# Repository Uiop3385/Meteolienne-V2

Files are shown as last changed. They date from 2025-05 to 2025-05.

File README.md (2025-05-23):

# Meteolienne-V2

A project aiming to create an extra-efficient wind turbine, that's able to spin around to face the wind, and includes several sensors to add weather station capabilities.

It's also capable of generating up to 10W of power, and is entirely self-sufficient, thanks to an on-board battery and solar panel, and a sleeping system to save power.

Here are some pictures:  
View from the bottom

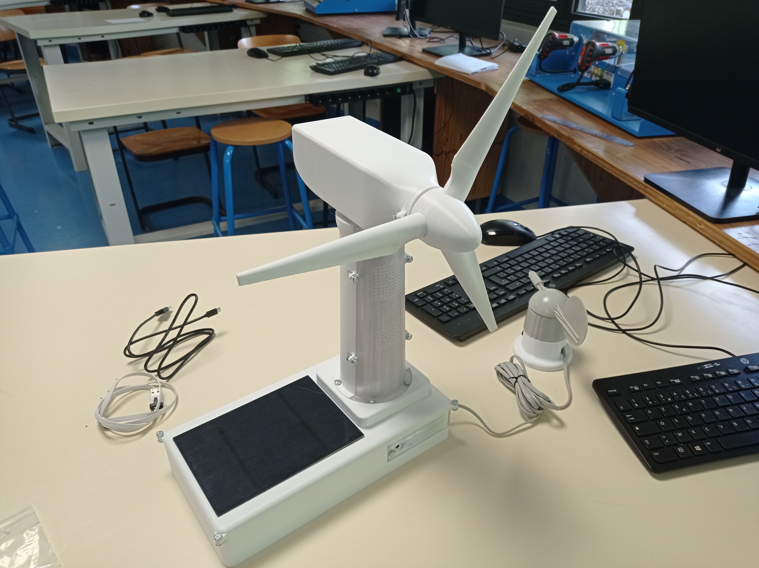
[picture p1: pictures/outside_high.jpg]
View from the top


## Disclaimer
If you're going to use any part of this project, please make sure you follow the terms of the licence. You can see a breakdown of them [here](https://choosealicense.com/licenses/mpl-2.0/).

## Info

This project is the successor to the [original Météolienne](https://github.com/Uiop3385/Meteolienne-V1) I've made. Compared to the first one:

- It's actually *somewhat* finished
- It communicates using WiFi and can be controlled through an app and web dashboard
- It implements the weather station capabilities
- It's far more energy efficient
- It generates power

The wireless connection is operated through Arduino IoT Cloud, using an Arduino MKR WiFi 1010 board. You'll need an account and a Maker subscription to make it work.

Some parts of this project, including variables in the code, part names in the CAD representation, etc, **are written in French**.

## Dashboards
Here are two images showcasing part of the two dashboards, the data one first, and the settings one after.

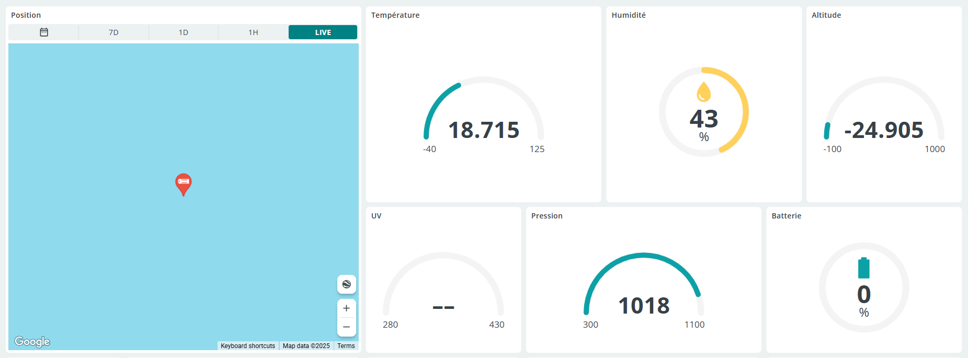
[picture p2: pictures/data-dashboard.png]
Data dashboard


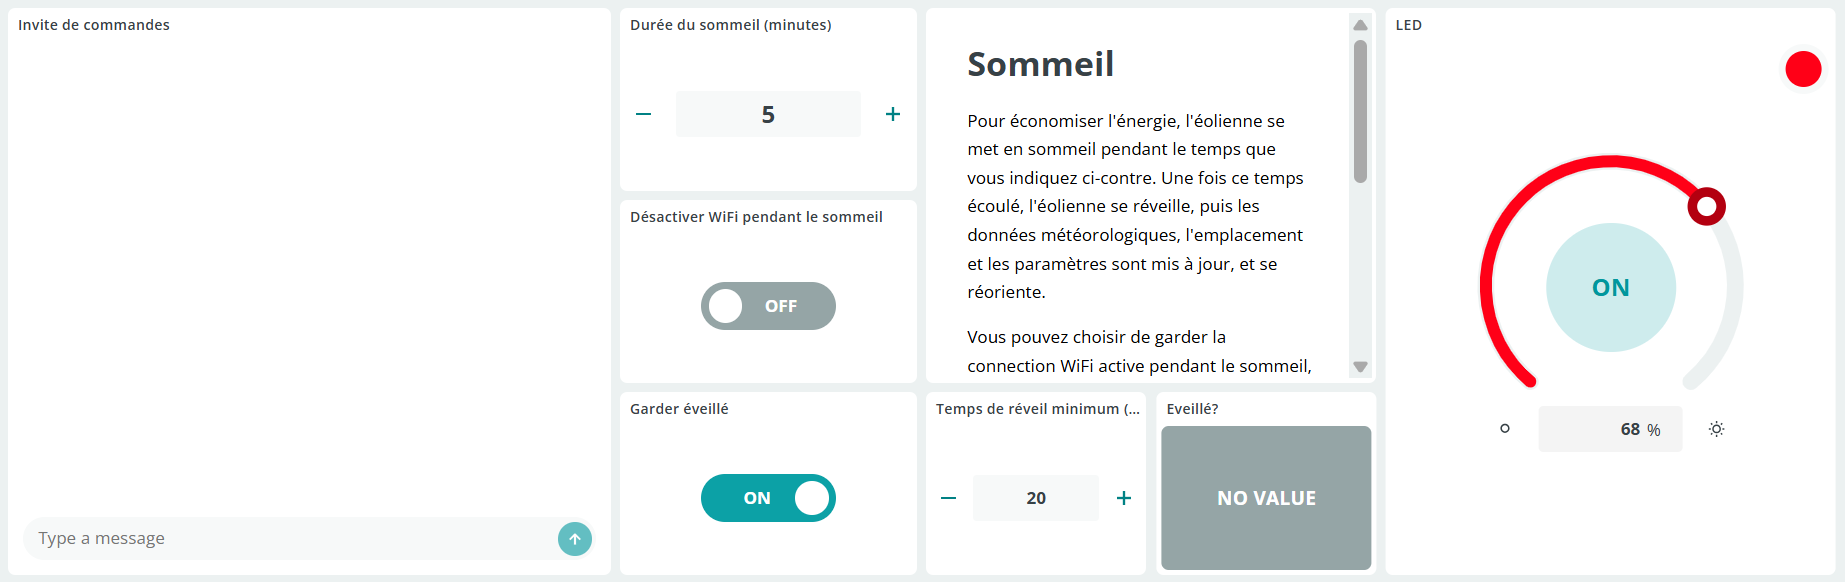
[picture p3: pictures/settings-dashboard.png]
Settings dashboard


These are the web dashboards. The mobile versions of them aren't shown here, but they're the same with a different layout to fit the size of a phone screen.

## Scripts
The files included in /scripts are not ready for use on the IoT Cloud editor. If you want to implement the code, dashboard, things and cloud variables, it's essential to use the template. If you're simply taking certain parts of the scripts, ignore this.

### Guide:
- Download meteolienne_template.tino in /scripts
- Access the Cloud Dashboard (https://app.arduino.cc)
- Go to Templates, then click on "Your Templates" at the top
- Select "Import local template (.tino)"
- Import the file you downloaded
- Then, press "Use template"
- You'll be asked to connect an Arduino MKR WiFi 1010

Once this is done, everything will automatically be copied over, and you're almost ready to upload! Just fill in the secrets tab with your WiFi credentials, and your ipdata API key for geolocation (you can get one free from their website, https://ipdata.co).

## Models
The entire wind turbine was modelled using Autodesk Fusion. You can access the .f3z from /models. If you're using a different CAD, there's also a .step you can use.

Alternatively, all parts of the wind turbine are available as .stl in /models/parts.

Render of the turbine from Fusion:
Realistic render of the wind turbine

The models were designed to be 3D printed. The ideal materials would be PETG and ASA, since they're strong, water resistant, and UV resistant. My prototype was made using PETG, with white filament for all parts but the mast cover and the IO shield. Those were printed in translucent filament.

## Components used
### Sensors
|Part name|Brand|Qty|
|--|--|--|
|MQ135 Air Quality sensor|Flying Fish|1|
|SEN0501 Environmental Sensor|DFRobot|1|
|NVGRLEX002 Wind vane + board|Lextronic|1|

### Other components
|Part name|Brand|Qty|
|--|--|--|
|C6045 Voltage Generator|cebekit|1|
|MKR WiFi 1010 board|Arduino|1|
|mBot Battery (Li-Po, 3.7V, 1800mAh)|Makeblock|1|
|28BYJ-48 Stepper Motor + Driver|N/A|1|
|S7V8F5 5V Voltage Regulator|Polulu|1|
|313070000 2.5W Solar Panel|Seeed Studio|1|

### Electronic components
|Type|Value/Ref|Qty|
|--|--|--|
|Resistor|220Ω|2|
|Resistor|1kΩ|4|
|Resistor|10kΩ|4|
|Resistor|15kΩ|2|
|Pushbutton|N/A|1|
|Capacitor|1000µF|1|
|LED|N/A|1|
|Diode|1N4007|6|
|Transistor|2N2222|4|

### Assembly parts:
|Type|ISO Reference|Value|Qty
|--|--|--|--|
|Bolt|ISO 4017|M4x10|19
|Nut|ISO 4035|M4|19|
|Screw|ISO 7046|M4x40|1|

And a bunch of jumper wires.

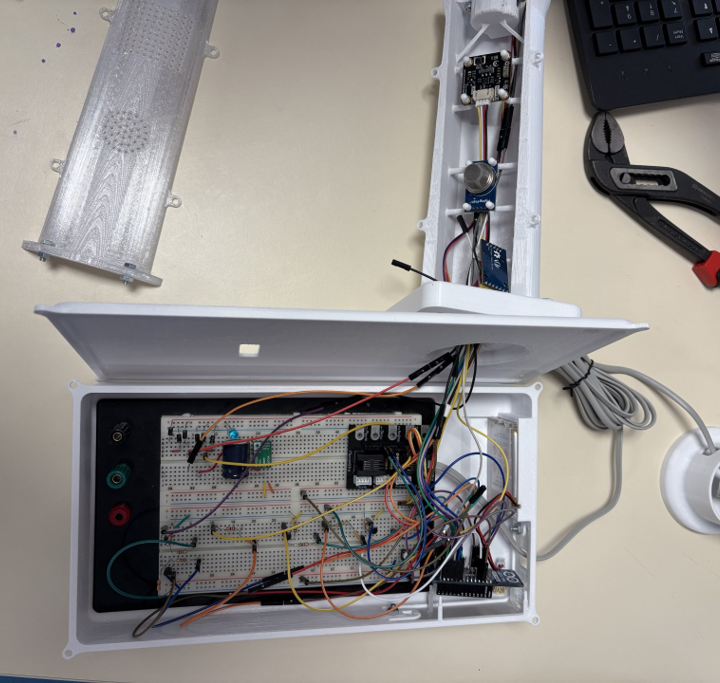
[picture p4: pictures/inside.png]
Inner wiring
Image of the inside:

## Oversights
While the project seems finished, there's still many things that are wrong with it. Here's a quick list of them:
- I can't actually get it to work. I'm unsure if the problem comes from my program or my board, but it won't let me upload it. The board no longer shows up on the computer outside of bootloader mode.
- Many components used rely on 5V, which I unsuspectingly hooked up to the 5V pin. However, this pin only outputs the 5V power coming from the USB. That means the board will never output this voltage from battery. The turbine is therefore not "self-sufficient".
- The wind near the ground is highly unstable. If you were to place the turbine on the ground, it would greatly struggle to pick up wind correctly. Not to mention, the wind vane would act very strangely too. It would need to be suspended much higher into the air for everything to function correctly.
- If wind speeds get too high, there's no protection to prevent the blades from spinning too fast and damaging the internals.
- There are several design flaws in my model. I only noticed them when assembling the turbine, and haven't fixed them since.
- Geolocation is, by design, highly inaccurate, since it's basing itself on IP address location. During testing, I could only ever get it to locate me in the same place in Germany (probably the location of the IoT Cloud servers). This could be mitigated by using Google's API.

## Assembly
I will not be providing any assembly instructions. You'll have to do with the information available here. Who would even want to recreate this anyway?

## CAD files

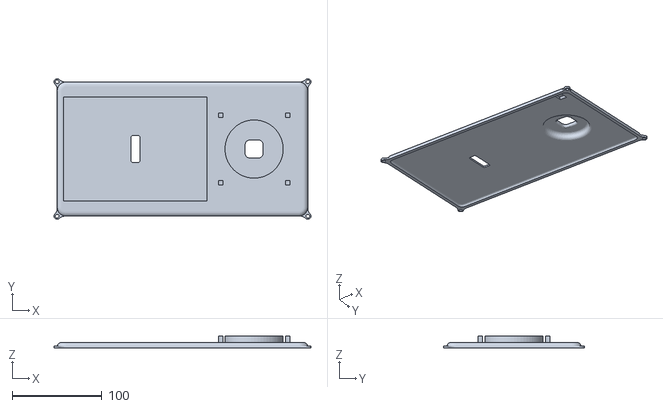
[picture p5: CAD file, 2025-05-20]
models/parts/Base Haute.stl
287.0 x 157.0 x 13.8

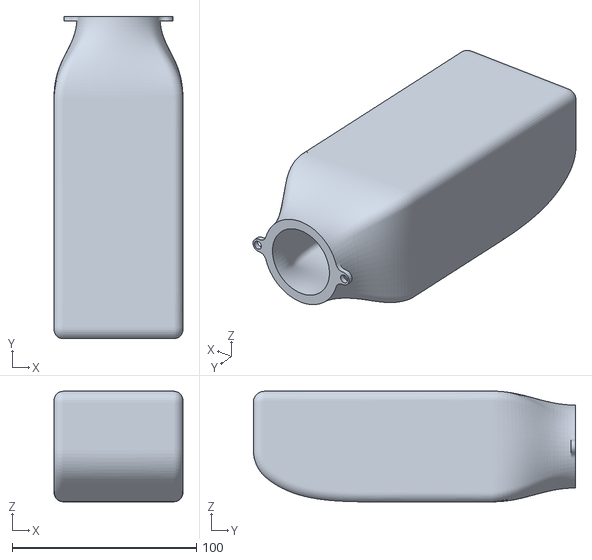
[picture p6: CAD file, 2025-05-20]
models/parts/Nacelle.stl
70.0 x 175.0 x 60.0

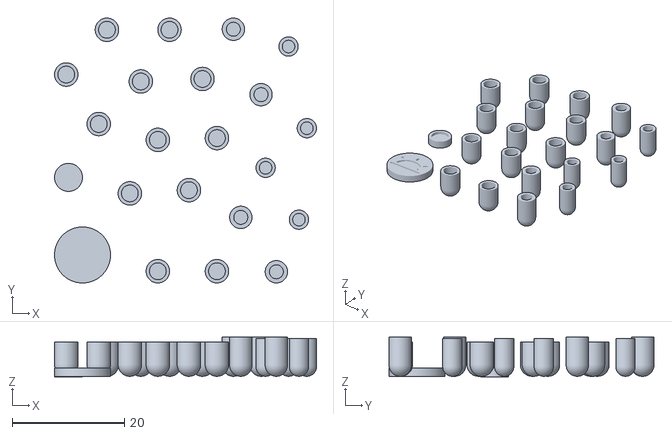
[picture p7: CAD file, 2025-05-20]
models/parts/Plaque Fixations v2.stl
46.8 x 47.3 x 7.10

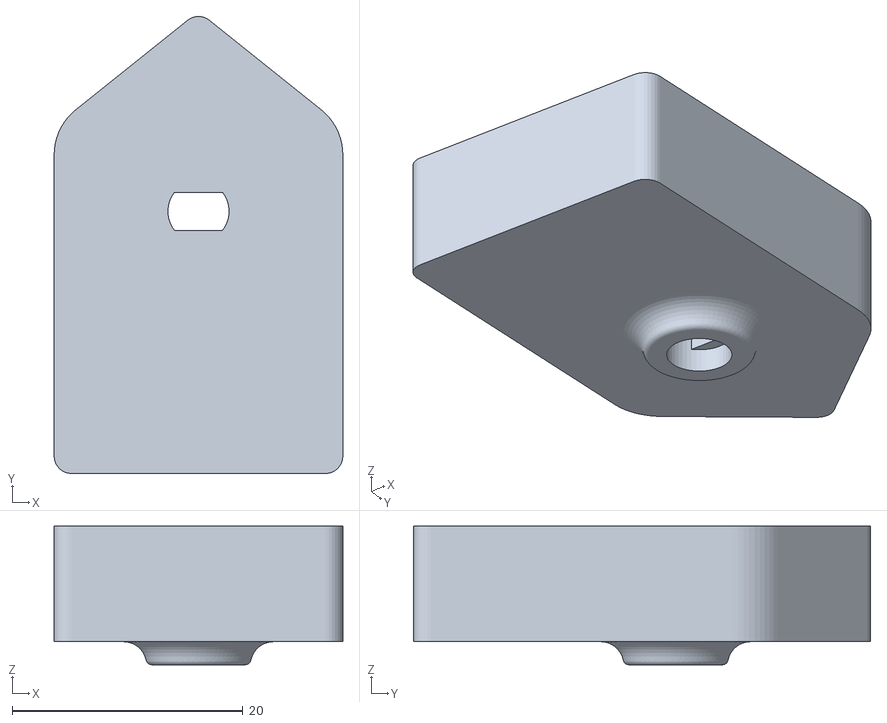
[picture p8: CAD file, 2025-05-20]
models/parts/Flèche.stl
25.0 x 39.6 x 12.0

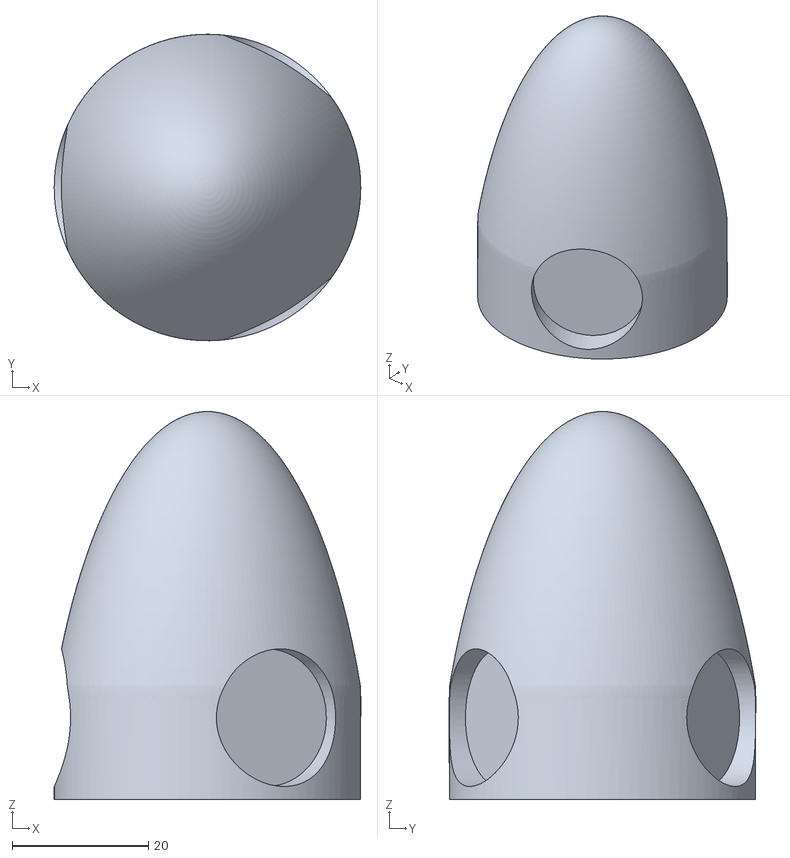
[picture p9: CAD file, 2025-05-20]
models/parts/Moyeu.stl
45.0 x 45.0 x 57.0

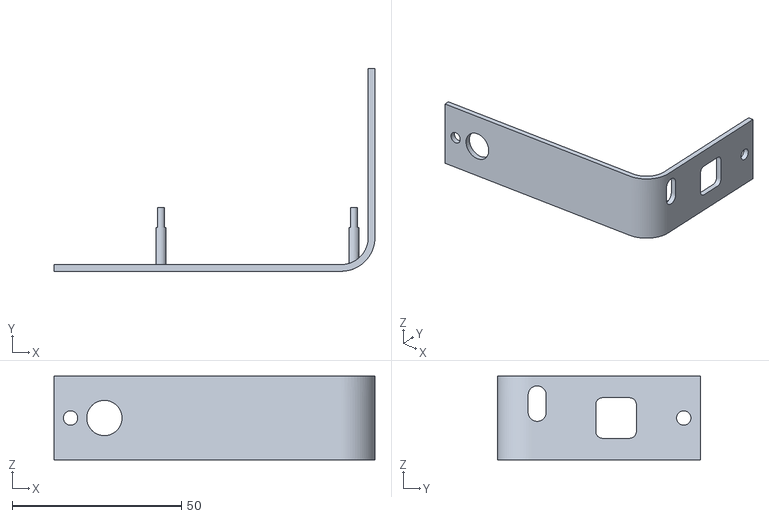
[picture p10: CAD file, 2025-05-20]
models/parts/IO Shield v2.stl
94.9 x 59.9 x 24.8

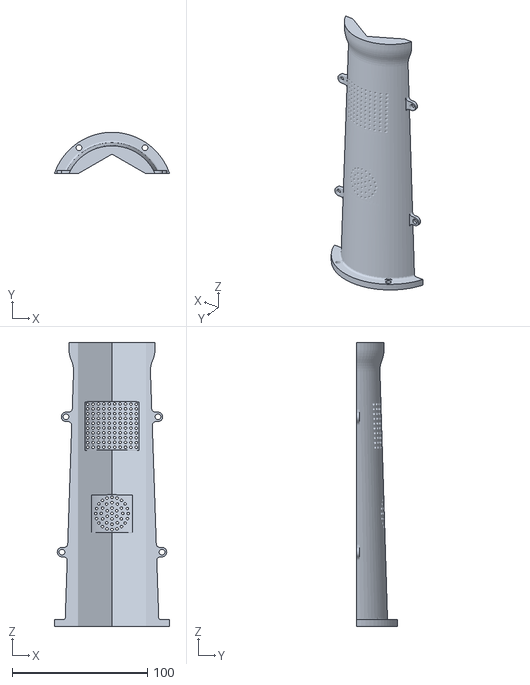
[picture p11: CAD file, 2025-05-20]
models/parts/Mât Secondaire.stl
85.2 x 30.5 x 210.0

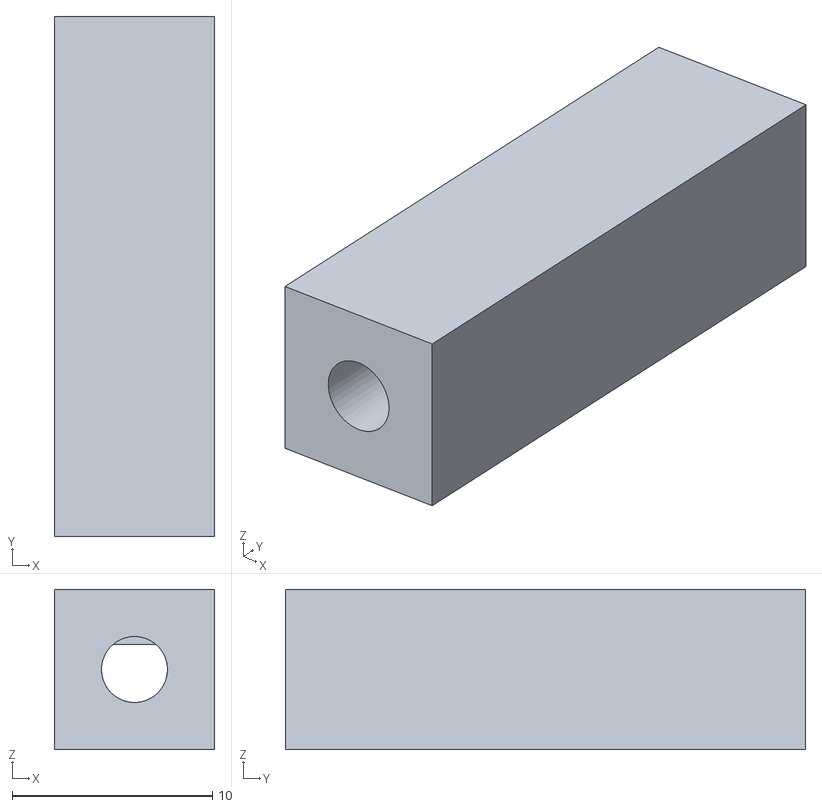
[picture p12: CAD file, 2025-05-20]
models/parts/Pavé.stl
8.00 x 26.0 x 8.00

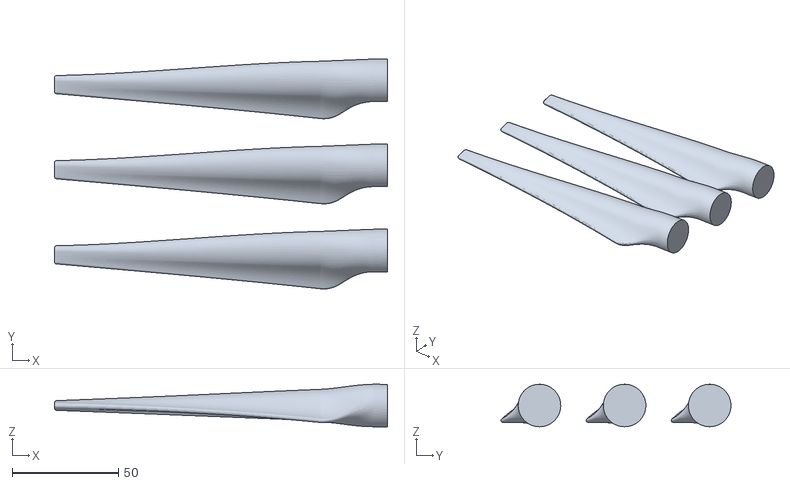
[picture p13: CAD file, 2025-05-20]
models/parts/Pales.stl
156.5 x 108.1 x 20.0

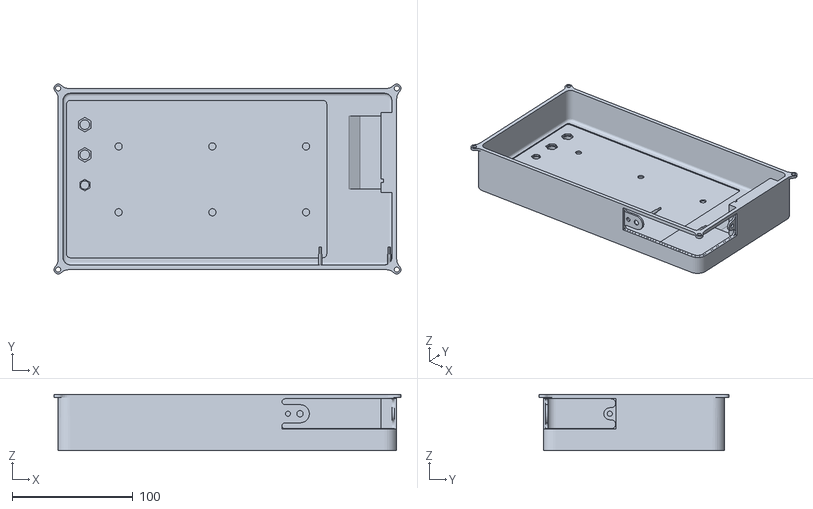
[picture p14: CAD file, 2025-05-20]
models/parts/Base Basse v2.stl
287.0 x 157.0 x 46.5

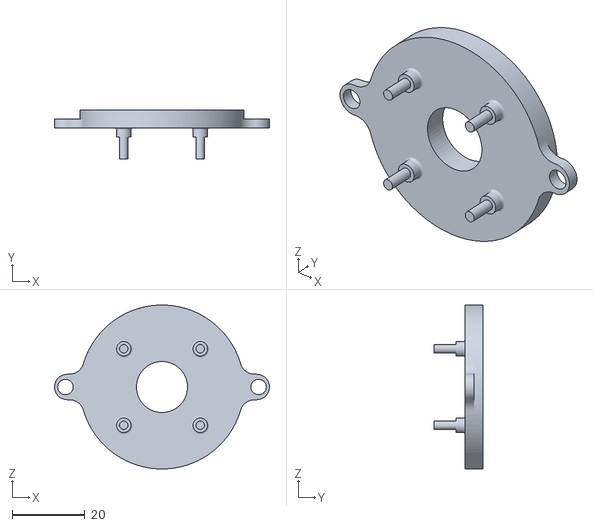
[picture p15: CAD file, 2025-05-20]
models/parts/Paroi Rotor 2.stl
59.0 x 13.5 x 45.0

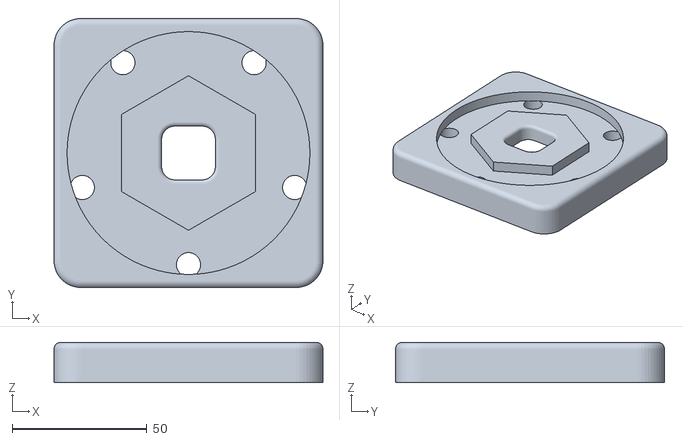
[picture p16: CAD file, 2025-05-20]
models/parts/Support Mât.stl
100.0 x 100.0 x 15.0

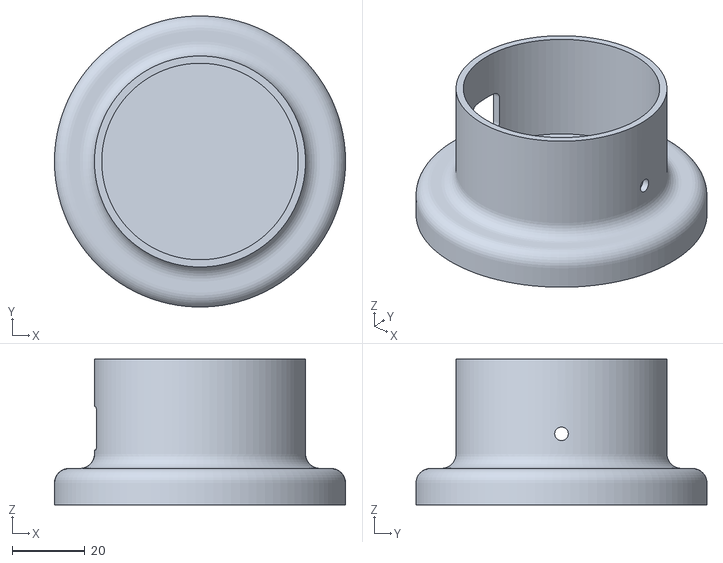
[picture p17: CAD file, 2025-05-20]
models/parts/Support Girouette.stl
80.0 x 80.0 x 40.0

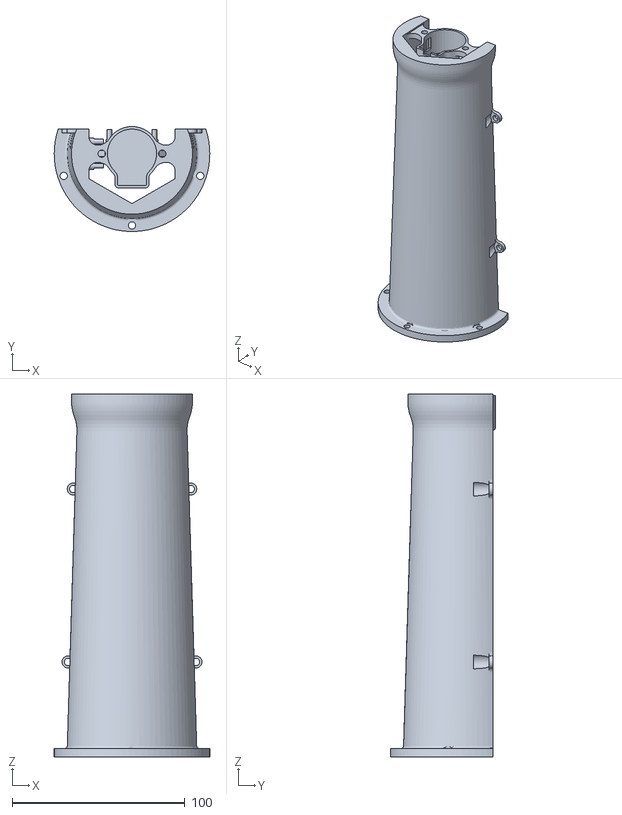
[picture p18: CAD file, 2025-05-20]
models/parts/Mât Principal.stl
90.0 x 60.7 x 210.0

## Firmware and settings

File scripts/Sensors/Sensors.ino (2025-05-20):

void updateEnvironmentalSensor() {
  temperature = environment.getTemperature(TEMP_C);
  pression = environment.getAtmospherePressure(HPA);
  humidite = environment.getHumidity();
  luminosite = environment.getLuminousIntensity();
  altitude = environment.getElevation();
  uv = environment.getUltravioletIntensity();
}

void updateAQSensor() {
  int co2_read = analogRead(aq_sensor_pin);
  co2 = map(co2_read, 0, 4096, 0, 100);
}

String queryPosition() {
  WiFiSSLClient client;
  int HTTPS_PORT = 443;
  String HTTP_METHOD = "GET";
  String response;
  char HOST_NAME[] = "eu-api.ipdata.co/";
  String PATH_NAME = String(WiFi.gatewayIP()) + String("?api-key=") + String(SECRET_GEOLOCATION_API_KEY) + String("&fields=latitude,longitude");

  if (client.connectSSL(HOST_NAME, HTTPS_PORT)) {
    Serial.println("Connected to server");
    
    client.println(HTTP_METHOD + " " + PATH_NAME + " HTTP/1.1");
    client.println("Host: " + String(HOST_NAME));
    client.println("Connection: close");
    client.println();

    while (client.connected()) {
      if (client.available()) {
        char c = client.read();
        response += c;
        Serial.print(c);
      }
    }

    client.stop();
    Serial.println();
    Serial.println("disconnected");
  } else {
    Serial.println("connection failed");
  }
}

void updatePosition() {
  String response = queryPosition();
  JsonDocument coordinates;
  DeserializationError error = deserializeJson(coordinates, response);
  if (error) {
    Serial.println("An error occurred during deserialization: "+String(error.c_str()));
  } else {
    float latitude = coordinates["latitude"] | 0.0f;
    float longitude = coordinates["longitude"] | 0.0f;
    String error_message = coordinates["message"] | "";
    if (latitude == 0.0 && longitude == 0.0) {
      Serial.println("An error occurred: "+error_message);
    }
    else {
      position = Location(latitude, longitude);
    }
  }
}

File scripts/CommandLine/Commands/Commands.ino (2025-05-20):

String macToString(byte mac[]) {
  String result = "";
  for (int i = 0; i < 6; i++) {
    if (mac[i] < 16) {
      result += "0";
    }
    result += String(mac[i], HEX);
    if (i < 5) {
      result += ":";
    }
  }
  return result;
}

String echoCommand(const String args[], size_t argCount) {
  String result = "";
  for (size_t i = 0; i < argCount; i++) {
      result += args[i] + " ";
  }
  result.trim(); // Modify result in place
  return result;
}

String infoCommand(const String args[], size_t argCount) {
  if (argCount == 0) {
      return "No arguments provided";
  } else {
      String response = "Arguments: ";
      for (size_t i = 0; i < argCount; i++) {
          response += args[i] + " ";
      }
      response.trim();
      return response;
  }
}

String locateCommand(const String args[], size_t argCount) {
  queryPosition();
  return "Location queried, check serial monitor.";
}

String positionCalibrateCommand(const String args[], size_t argCount) {
  int8_t target_position = constrain(args[0].toInt(), 0, 15);
  updateRotation(target_position);
  return "Calibrated to position " + String(current_position) + ".";
}

String stepCalibrateCommand(const String args[], size_t argCount) {
  int16_t steps = constrain(args[0].toInt(), 0, 15);
  stepper.step(steps);
  setCurrentPosition(0);
  return "Calibrated by " + String(steps) + " steps.";
}

String resetCommand(const String args[], size_t argCount) {
  NVIC_SystemReset();
  return "Reset.";
}

String sleepNowCommand(const String args[], size_t argCount) {
  uint8_t duration = (argCount == 1) ? constrain(args[0].toInt(), 1, 120) : 0;
  sleepRoutine(duration);
  return "Went to sleep.";
}

String wifiLpmConfigurationCommand(const String args[], size_t argCount) {
  if (constrain(args[0].toInt(), 0, 1) == 0) {
    WiFi.noLowPowerMode();
    return "Low Power Mode has been disabled.";
  } else {
    WiFi.lowPowerMode();
    return "Low Power Mode has been enabled.";
  }
}

String wifiScanNetworksCommand(const String args[], size_t argCount) {
  int numNetworks = WiFi.scanNetworks();
  String result = "List of available networks:\n";

  if (numNetworks == 0) {
    result = "No networks found.";
  } else {
    for (int i = 0; i < numNetworks; i++) {
      result += "ID: " + String(i);
      result += ", SSID: " + String(WiFi.SSID(i));
      result += ", RSSI: " + String(WiFi.RSSI(i)) + " dBm\n";
    }
  }
  return result;
}

String wifiPingCommand(const String args[], size_t argCount) {
  String hostname = args[0];
  int ping = WiFi.ping(hostname);
  if (ping >= 0) {
    return "Successfully pinged "+hostname+" in "+String(ping)+"ms!";
  } else {
    return "Something went wrong. Error code: "+String(ping);
  }
}

String wifiGetDebugInfoCommand(const String args[], size_t argCount) {
  String response = "Wifi debugging information log:\n";
  response.concat("Network SSID: "+String(WiFi.SSID())+"\n");
  response.concat("Network signal strength (RSSI): "+String(WiFi.RSSI())+"\n");
  response.concat("Encryption used: "+String(WiFi.encryptionType())+"\n");
  response.concat("Connection status: "+String(WiFi.status())+"\n");
  response.concat("Wifi firmware version: "+String(WiFi.firmwareVersion())+"\n");
  response.concat("Local IP address: "+String(WiFi.localIP())+"\n");
  response.concat("Subnet mask: "+String(WiFi.subnetMask())+"\n");
  response.concat("Gateway: "+String(WiFi.gatewayIP())+"\n");
  response.concat("Primary DNS: "+String(WiFi.dnsIP())+"\n");
  response.concat("Secondary DNS: "+String(WiFi.dnsIP(1))+"\n");
  byte mac[6];
  WiFi.macAddress(mac);
  response.concat("Local MAC address: "+macToString(mac)+"\n");
  byte bssid[6];
  WiFi.BSSID(bssid);
  response.concat("Router MAC address (BSSID): "+macToString(bssid));
  return response;
}

String wifiGetReasonCodeCommand(const String args[], size_t argCount) {
  return "Deauthentication reason code: "+String(WiFi.reasonCode());
}

String demoSpinCommand(const String args[], size_t argCount) {
  updateRotation(15);
  updateRotation(-15);
  return "Spin demo executed successfully!";
}

String demoLedBuiltinCommand(const String args[], size_t argCount) {
  static bool state = LOW;
  state = !state;
  digitalWrite(LED_BUILTIN, state);
  return "Built-in LED state updated!";
}
